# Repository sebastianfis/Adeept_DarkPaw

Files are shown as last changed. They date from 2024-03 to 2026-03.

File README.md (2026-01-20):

# DarkPaw

My personal take on improving the Adeept Dark Paw robot. Specific features I aim to tackle:
* **Correct Kinematic model**
* **AI supported object recognition/tracking**
* **Create an autonomous mode with dedicated behaviour**
* **Update the robot control interface**
* ~~**Voice recognition**~~ -> abandoned for now
* ~~**Sound generation**~~ -> abandoned for now

## UPDATE 2026-01-20:
As usual, it has been quite some time since I wrote the last update :sweat_smile: : 

### Hardware and hardware integration:
Long term testing showed, that the original 25 W power supply I intended to use, is too weak to run the Raspi5 with AI 
Hat and the ESP and the LEDs and all the servos. So I switched the power supply for something bigger and added a third 
18060 battery to power the whole thing for a decent amount of time (integration of the batteries pending). 

This led to a new issue: The ESP would not boot at the same time as the Raspi, which was never a problem before 
(Either its voltage ripple or some weird grounding issue of the power supply). I was able to solve this by starting 
up the ESP and using one of its outputs to switch on the RASPI via a MOSFET relays, so they now boot in sequence.

I also added a watchdog to the communication, so the ESP would detect a software crash on the Raspi side and stop 
instead of coniuting the last given command!

### Correct Kinematic model
I did some quite extensive testing on the C++ Implementation. The ESP32 works like a charm and is very reliable!

### AI supported object recognition/tracking
I added some code for object movement detection and in the process discovered, how unreliable the distance sensor 
readings are. Since on the Raspi 5 the Chip architecture is fairly different, hardware timed GPIO is not availlable.
Since regular GPIO timing in Python is not the most precise, I had to switch the distance sensor implementation to 
gpiod and add a bunch of stuff (floating average mean, rejection of false trigger events, sanity checks on timing and 
disatnce values). This is now as good, as it's going to get while running directly on a Pi. I also discovered that 
regular updates to the selected target data were missing, which is mandatory for the movement check.

### Robot control Interface website
Tested now and fully functional.

### What's next?
I am quite satisfied with the hardware as it is now (battery integration still pending). Also the C++ implentation is 
rather solid now and the Robt Control interface website (while it is not the most beautiful site) is very functional 
and highly responsive. From the original project goals, only **Create an autonomous mode with dedicated behaviour** is 
not complete yet, so that is where i can finally put my focus on.

## UPDATE 2025-04-26:
It has been quite some time since I wrote the last update and quite a few things have changed in the meantime :sweat_smile: : 

### Hardware and hardware integration: 
I designed some 3d printed parts to implement the changes I had to do in terms of hardware positioning. Check out the 
3d planning folder for the models, if you think you can use them.

### Correct Kinematic model
I did not have the time for a proper test of the C++ Implementation, yet. All I know right now is, that the serial 
communication works, so the C++ programm on the ESP is running fine, but I have not seen any actual movement from 
the robot yet. Have to do more tests on an isolated part of the setup to bugfix this.

### AI supported object recognition/tracking
Using the RASPI 5 and the AI HAT is very cool. I can now run the newest yolov11m model on the Hailo with ~18 fps 
framerate! 

### Robot control Interface website
While running the detection code locally gave me pretty good framerates, they plumeted to ~ 3 fps, when I was using 
the Webserver. Clearly streaming a MJPEG to a flask server is not the best choice for this task. In the end, I was 
forced to go a completely different route. There is a good reason, that both Hailo and Raspi Camera have a good load 
of GStreamer examples in ther repos. Gstreamer is probably one of the best choices, if you want to stream actual video 
(in contrast to an image sequence) over the web. But the python bindings for that are not well documented and the 
string based pipeline concept can be hard to grasp in the beginning. Since Hailo has a repo, where they only use 
gstreamer instead of Python for the whole chain of captureing an image, runing inference, annotation, and finally 
displaying/streaming, I gave that implementation a try. It turned out to be slower and not as pretty, as the 
implementation I had before using Raspicam2 and Supervision code, so I quickly gave up on that. So the new architecture 
is the following:

Raspicam2 -> inference & frame annoation as videosrc -> Gstreamer Pipeline -> WebRTC as videosink -> display on webpage

Took me a while to get this running, but it finally does! Bonus of this: Through WebRTC, asyncio and aiohttp I can also 
create a VERY responsive data channel for sending measurement data to the control interface and receive comands from 
it's elements.

## UPDATE 2024-12-08:
It has been quite some time since I wrote the last update and quite a few things have changed in the meantime :sweat_smile: : 

### Hardware
Time flies and when I started this project, the Google Coral Dev Board Mini or the Google Coral USB Accelerator were 
the only viable options for hardware accelerated AI applications on a size compatible with the Dark Paw robot frame. 
Well, there was the NVidia Jetson Nano, but I found that one too expensive and a bit too power hungry.

With the Raspberry Pi 5 and the Hailo AI HAT now on the market, there are is now actually a better option availlable 
considering the following criteria:
* Computing performance (in terms of TOPS)
* Model input tensor size (= image resolution) for yolo models
* Compatibility with peripheral equipment 
* Development comfort for video applications on a non-headless system
* Product support: There seems to have been no update to the Mendel Linux OS for the past 3 years...

Since I was never really quite satisfied with the object detection performance I was able to achieve with the Coral Dev Board Mini, I've chosen to switch the hardware for a Raspi 5 with an AI HAT. I felt the 13 TOPS variant would be suffcient and would safe some power vs. the 26 TOPS variant. This does not change anything on the planned "fore brain" / "hind brain" separation. I still think it is a good idea to do that separation!

I also added a HC-SR04 ultrasonic distance sensor. This will allow the robot to move in on an object down to a certain distance and even keep the distance for a moving object. And to make the robot a bit more expressive, I exchanged the blue LED of the front lens with a WS2812b multi-colour LED, that can be chained to the internal LEDs of the robot.

### Hardware Integration
Switching to the Raspi 5 / AI HAT Architecture has one downside though: It will be a lot bigger, than the Coral Dev Board Mini. So I had to do some re-arrangements of the robots insides: The LED-PCBs have to be moved further outside. The RASPI 5 and the AI HAT will be positionend on one side of the vertical electronics holder, while the ESP32 and the I2C PWM Servo Controller will be positioned on the other side. It's a close fit and I will probably curse a lot during cabling of this, but it should fit. I also won't ba able to fit the power supply inside the robot anymore, so I added an add-on part for the robot to carry a new DF-robot power supply PCB on its aft-side (this should come in handy in case of a robot spider uprising :joy:). Finally I added a holder to the HC-SR04 ultrasonic distance sensor to the upper front of the robot.

### Correct Kinematic model
I was able to port the python implementation to C++ and run it on an ESP32. It runs without crashing, and first tests on the calculated values are very promising. However, it is still lacking a real life test with the servos connected.

For communcation I will try using the good old serial connection first. This will run with minimal overhead both on the Raspi and the ESP32.

### AI supported object recognition/tracking
I was never really quite satisfied with the performance of the object detection models of the Google Coral Model Zoo on the Google Coral Mini board. The models were either too slow for real time video detection or accuracy was not satisfactory. So I went looking for more cutting edge object detection models and stumbled upon the yolo model series and later also ssd_spaghettinet. However, with these newer models some internal architecture of the Edge TPU limits the input tensor size, with which the model will still compile to run entirely on the Edge TPU to rather low resolutions. This means that object detection performance was better than with the models from the Coral model zoo, but false detection rates were still higher than what I had hoped for. Also, the limited resolution would make the robot a bit "short-sighted". It did work with an acceptable frame rate and I even got a tracker akgorithm to work, whcih would allow for keeping IDs of objects across different frames.

In the meantime, HAILO released a dedicated AI HAT for the Raspberry Pi 5, which does not have this limitation on input tensor size for modern object detection architectures. It also exceeds the TPU computing power by a factor > 3 (13 TOPS on the HAILO-8L vs. 4 TOPS on the Google Coral Dev Board Mini). So I decided to switch hardware (see above) and go ahead with a Raspi 5 equipped with an AI HAT. Getting the models to run in the Raspi Eco system was rather straightforward based on the examples in the picamera2 Repo and the HAILO Raspi 5 examples. This inculdes a object tracking algorithm with really awesome performance. 

### Autonomous mode with dedicated behaviour
No update on this (yet), except that I included 
* A "patrol" mode: The robot will go back and forth, with some tolerance on the angles, so it won't always go back and forth on the same path
* A "dance" mode: LEDs will set a light show and the robot will assume different poses at a certain rythm. This one is actually already finished :joy:

### Robot control Interface website
Oh boy! I put that off for quite some time. Understanding how the code of the Adeept Dark Paw original interface works was almost impossible to me. At some point I understood, that it was built in some sort of .js environment (I think Vue.js), but that did not make it much easier for someone with 0 experience in frontend development. In the end I gave up on trying to understand what the original code was trying to do and decided to do my own thing. 

So I started with designing a html/css website with Grapes.js and wrote my own javascript middleware. Putting that in contact with a flask server and responsive video streaming was everything but easy. There are numerous examples for simple video streaming out there, but most will reload the entire webiste over and over again, making registration of input commands a gamble at best. I finally found a solution for that and wrote a class-wrapped webserver implementation with thread-save command and data passing.

## UPDATE 2024-02-11:
After abondening the project for quite some time I took it up again. Here are some thoughts I had in the meantime 
(some of those caused my abandoning the project originally :sweat_smile:): 
### Hardware
Its pretty clear that the original Raspi based hardware would not be able to sustain all the features I'd like 
the robot to have. Checking the capabilities of availlable hardware, I decided that I would go with a Google 
Coral Mini board instead as main computation device, due to its on-board TPU, making it a great choice for 
AI applications.

However, after playing around with the Google Coral board I realized, that even with the on-board TPU there
would be issues with realization of all the stuff I wanted to implement, mainly because it would not be able 
to run several pre-compiled models (object recognition/tracking + Voice recognition + Sound generation) in 
parallel, but also since even running object recognition/tracking alone is already rather slow on the board.

So I had to narrow the project down on the points that were most important to me: 
* **Correct Kinematic model**
* **AI supported object recognition/tracking**
* ~~**Voice recognition**~~ -> abandoned for now
* ~~**Sound generation**~~ -> abandoned for now
* **Create an autonomous mode with dedicated behaviour**

Also, python is not the ideal programming language for "number crunching" which is essential for a 
correct kinematic model. With the lags I had seen on the Coral board, I decided to give the robot a "hind brain". 
Think about it: When you want to lift your extended arm, you do not think: 
* check shoulder angle, 
* check elbow angle
* calculate angle difference shoulder
* calculate angle difference elbow
* execute necessary angle changes

All you think is: "Lift and extend arm". All the rest: the fine adjustments, the translations into explicit 
control signals to all the muscles involved, the correct timing of the movements, etc... that's all done by 
your hind brain, without you having to take care of it. Why not mimick that separation of tasks in the robot 
as well? 

So the plan is to share the load between two computing entities: The main behaviour algorithm and AI supported 
object recognition/tracking would run on the "fore brain", which is the Google Coral board. As "hind brain" I am 
thinking about using somthing like an ESP32 (tbc). Running the number crunching kinematics on the ESP in C++ 
makes it efficient and fast. From there, Servo control should be pretty straight froward through a I2C connected 
PWM controller.

Considering how the two "brain-parts" will communicate with each other, I thought about using a serial exchange. 
But maybe I'll use the ROS2 environment instead, since it already provides a framework for communication of 
different computing nodes.

### Correct Kinematic model
If you checked out the implementation size of the kinematic model, you might wonder why It is so huge. 

The answer is simple: The availlable robot control packages I found out there while researching (e.g. ROS2) are 
limited to linear kinematic models. This is well and good for most applications, but the Adeept Dark Paw robots 
construction relies heavily on four bar linkage mechanisms (check out [this page](https://www.geogebra.org/m/BueCG9ch)
for an interactive animation).

Such a mechanism can be extremely strong, but is **highly non-linear**, especially with several of these 
actuators linked together, as it is the case here. Also, there are limits to the acutators, where further 
increase of the actuated parameter (aka servo angle) would actually lead to a decrease of the desired effect 
(e.g. retraction of the foot, even though a linear model would predict further extension).

So that's why I had to write the code from scratch to get a truely correct kinematic model. 

The model was already working quite well in Python, when I stopped working on the project, but I 
decided to add some details to the test visualizations (e.g. making them full 3d and build up on one another).

The next step will be to re-implement the tested python code in C++. In principle easy, but I have not yet 
written code containing class definitions in C++. But I'm hoping ChatGPT will help me out there :grin:

### AI supported object recognition/tracking
I already played around a bit with the Google Coral board and think it should work. I just have to find out, 
how I want to do the integration with the overall behavior algorithms, but more on that later

### Autonomous mode with dedicated behaviour
I actually started working on that part by drawing out the logic in a block flow diagram, but it is far 
from being finished...

## UPDATE 2024-02-23:
### Correct Kinematic model
Ok, so Kinematics works like a charm and I managed to implement all possible poses. However, I noticed 
a few unexpecetd challanges:

* From the "standard" leg position, movement range in y is VERY limited. I don't think that there's 
much can be done about it. It's a result of the kinematics. The only workaround for that is to let it do smaller 
steps in faster succession in y direction (move left/right). This also means, that I will not be able to make 
the robot circle an external reference point (like an identified object, it finds interesting and wants to 
take a closer look).
* The COG of the robot seems to be badly balanced. The poses, where it lifts a single leg are very 
unstable (and this means it does wobble a lot when walking as well). I'll have to do some more tests, 
this is true for all legs and if it can be counterbalanced. Another explanation might be the inertia of 
setting a pose too quickly. This can be easily changed, as the implementation allows for intermediate 
samples.

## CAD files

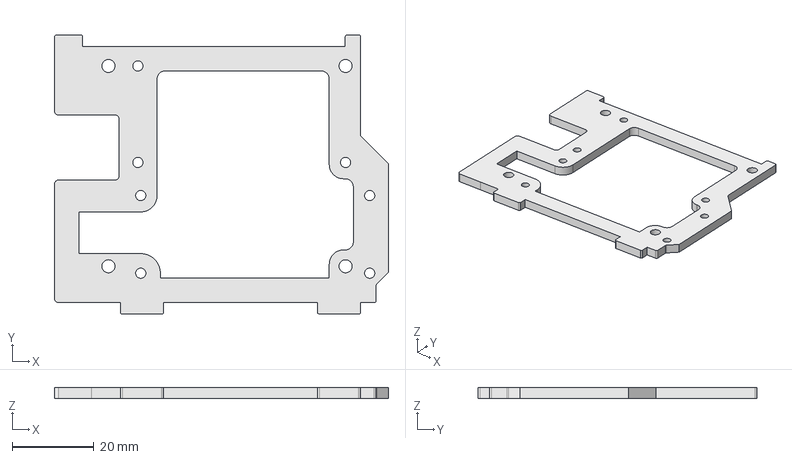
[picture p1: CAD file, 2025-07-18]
3d_planning/electronics_holder_new.FCStd
81.7 x 68.3 x 2.80 mm

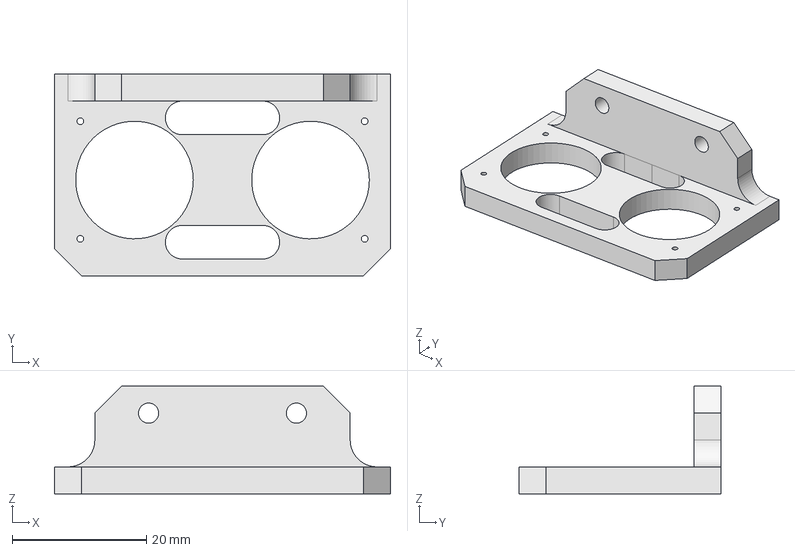
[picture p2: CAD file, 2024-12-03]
3d_planning/Ultrasonics_holder2.FCStd
50.0 x 30.0 x 16.0 mm

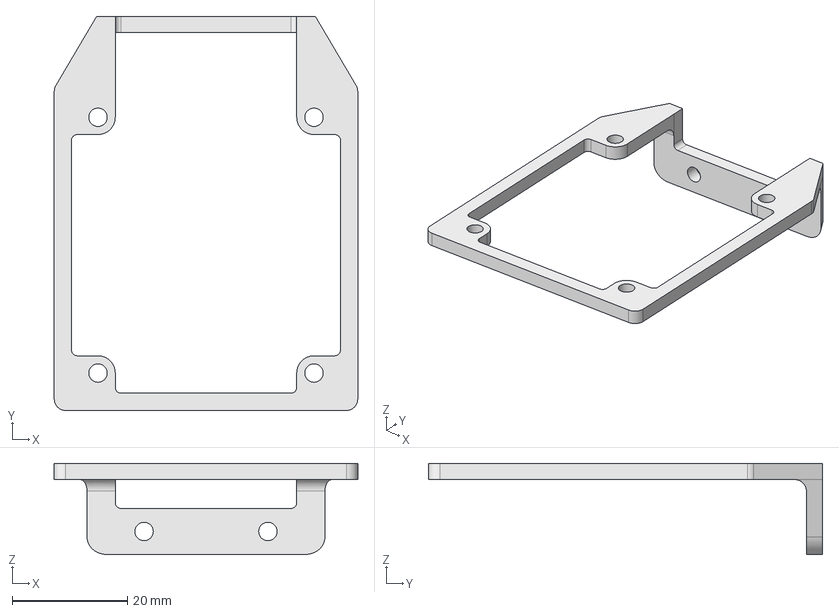
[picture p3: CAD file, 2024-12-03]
3d_planning/Powermodule_holder.FCStd
52.7 x 68.4 x 15.8 mm

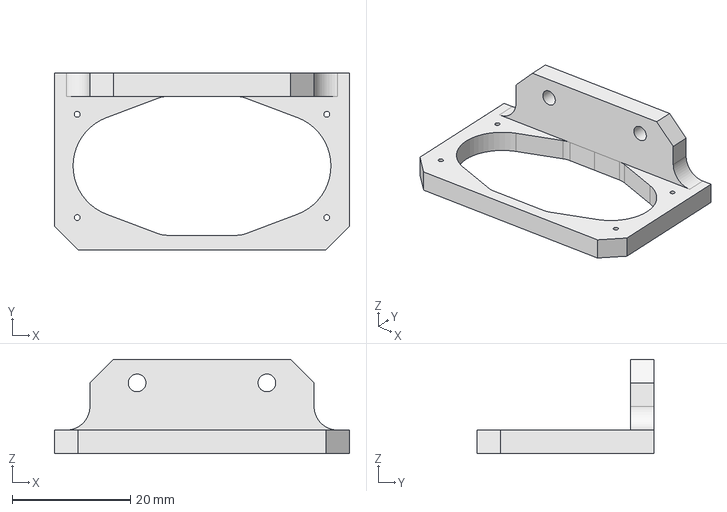
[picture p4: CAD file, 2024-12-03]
3d_planning/Ultrasonics_holder.FCStd
50.0 x 30.0 x 16.0 mm

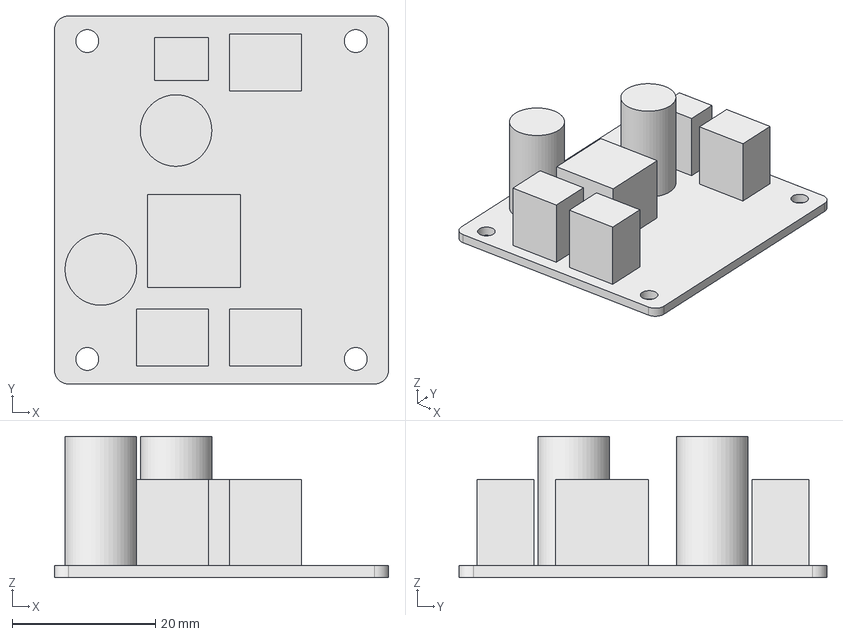
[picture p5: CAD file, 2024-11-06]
3d_planning/DF_robot_Powermodule.FCStd
46.7 x 51.4 x 19.7 mm

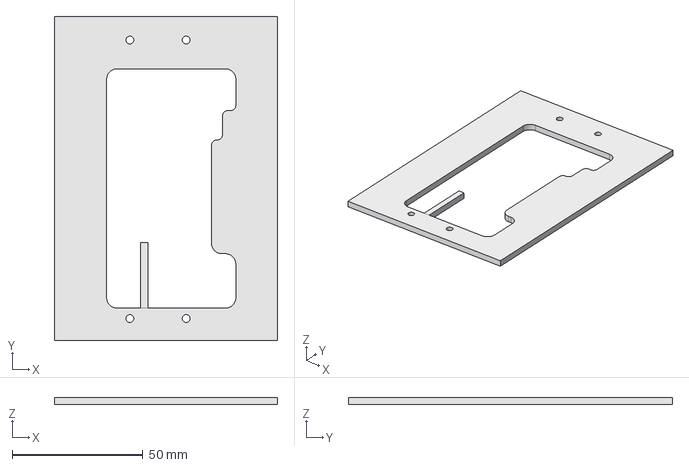
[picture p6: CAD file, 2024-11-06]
3d_planning/intermediate_boundary.FCStd
85.4 x 123.9 x 2.80 mm

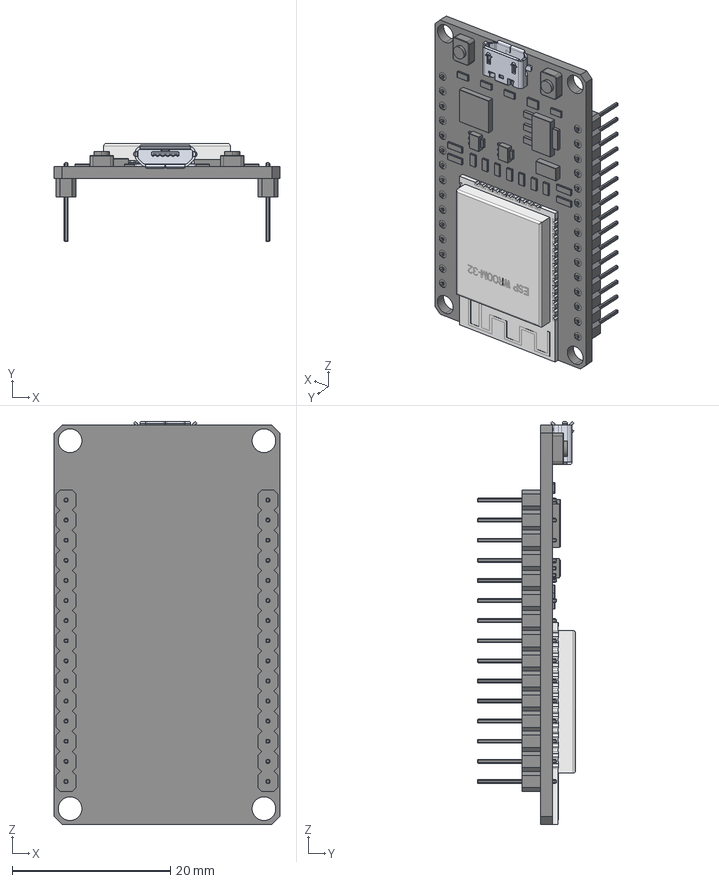
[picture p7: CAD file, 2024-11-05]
3d_planning/ESP32_Microcontrollerboard.FCStd
28.5 x 12.4 x 50.9 mm
micro_usb_47346-0001
ESP-WROOM-32
6.ESP-32_Predeterminado
6.ESP-32_Predeterminado001
6.ESP-32_Predeterminado002
6.ESP-32_Predeterminado003
6.ESP-32_Predeterminado004
6.ESP-32_Predeterminado005
6.ESP-32_Predeterminado006
6.ESP-32_Predeterminado007
6.ESP-32_Predeterminado008
6.ESP-32_Predeterminado009
6.ESP-32_Predeterminado010
6.ESP-32_Predeterminado011
6.ESP-32_Predeterminado012
6.ESP-32_Predeterminado013
6.ESP-32_Predeterminado014
6.ESP-32_Predeterminado015
6.ESP-32_Predeterminado016
6.ESP-32_Predeterminado017
6.ESP-32_Predeterminado018
6.ESP-32_Predeterminado019
6.ESP-32_Predeterminado020
6.ESP-32_Predeterminado021
6.ESP-32_Predeterminado022
6.ESP-32_Predeterminado023
6.ESP-32_Predeterminado024
6.ESP-32_Predeterminado025
6.ESP-32_Predeterminado026
6.ESP-32_Predeterminado027
6.ESP-32_Predeterminado028
6.ESP-32_Predeterminado029
6.ESP-32_Predeterminado030

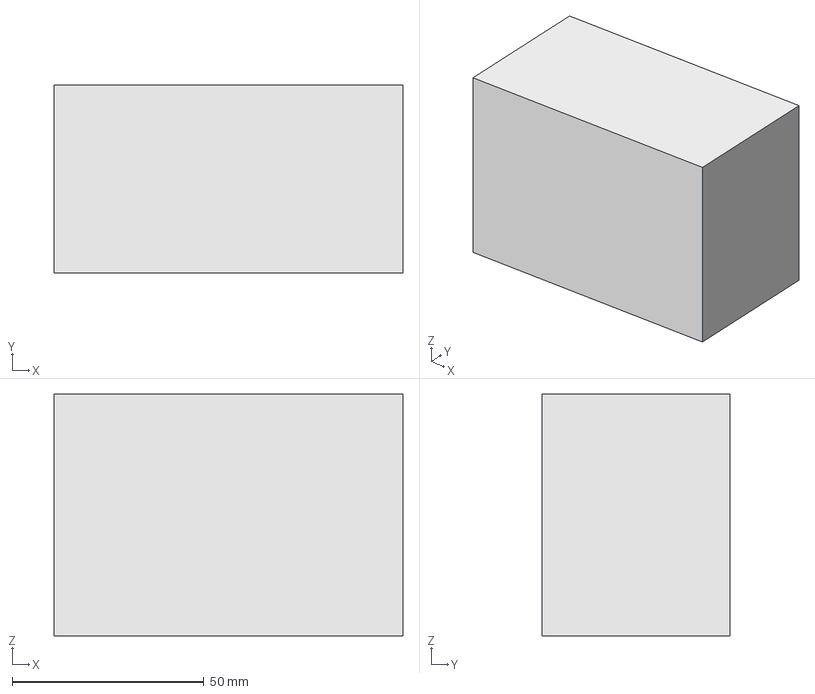
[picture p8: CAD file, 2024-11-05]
3d_planning/free_electronics_volume.FCStd
91.0 x 49.0 x 63.0 mm

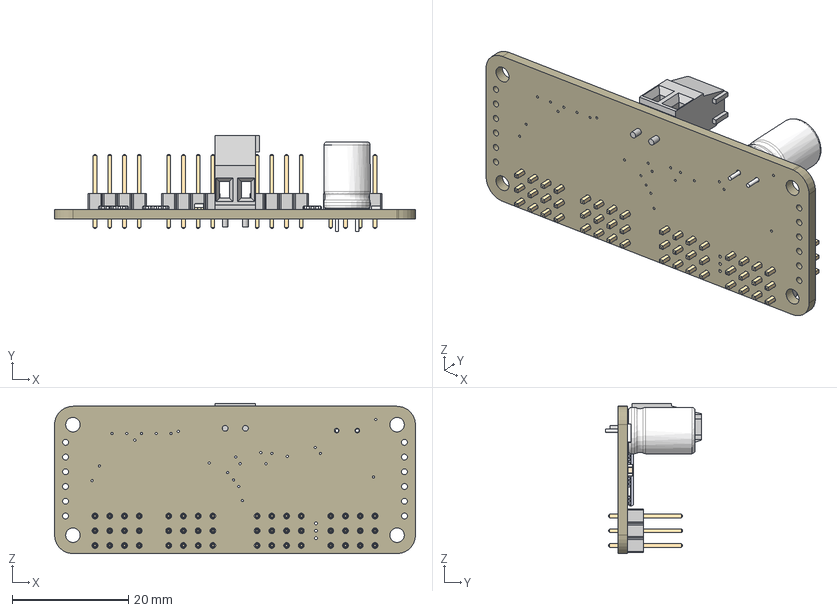
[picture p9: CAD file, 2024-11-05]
3d_planning/PCA9685_Servo_controller.FCStd
62.2 x 16.6 x 25.9 mm
Board
Pins
Pins001
Pins002
Pins003
Case
Pins005
Pins006
Pins007
Pins008
Case001
Pins010
Pins011
Pins012
Pins013
Case002
Pins015
Pins016
Pins017
Pins018
Case003
Pins020
Pins021
Pins022
Pins023
Case004
Pins025
Pins026
Pins027
Pins028
Case005
Pins030
Pins031
Pins032
Pins033
Case006
Pins035
Pins036
Pins037
Pins038
Case007
Pins040
Pins041
Pins042
Pins043
Case008
Pins045
Pins046
Pins047
Pins048
Case009
Pins050
Pins051
Pins052
Pins053
Case010
Pins055
Pins056
Pins057
Pins058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

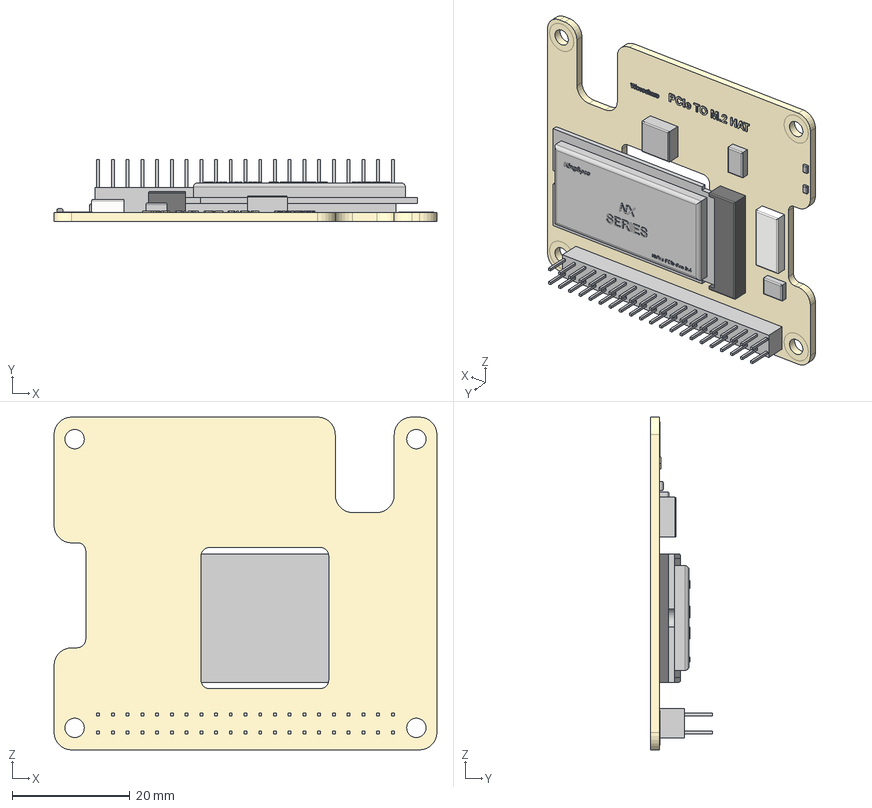
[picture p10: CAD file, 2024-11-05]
3d_planning/Raspi5_HAT.FCStd
65.0 x 10.6 x 56.5 mm
PCIe M.2 HAT Model
M.2 Connector
PCIe connector
Misc IC's
Misc IC's001
Misc IC's002
Misc IC's003
Misc IC's004
Misc IC's005
2242 NVMe

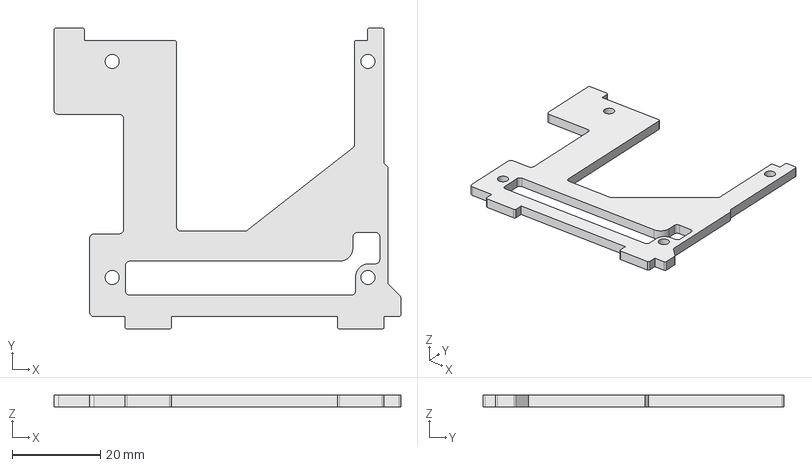
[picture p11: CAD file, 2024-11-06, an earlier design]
3d_planning/electronics_holder_old.FCStd
78.7 x 68.3 x 2.80 mm

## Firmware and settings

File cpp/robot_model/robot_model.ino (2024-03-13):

// #include "FourBarLinkage.h"
#include "math.h"
#include "SpiderLeg.h"
#include "Gait.h"
#include "Pose.h"

// FourBarLinkage linkage(42.5, 14.5, 38, 27.8, 90);
SpiderLeg RF(1, 1, "RF");
SpiderLeg LF(1, -1, "LF");
SpiderLeg RB(-1, 1, "RB");
SpiderLeg LB(-1, -1, "LB");

SpiderLeg *leg_list[] = {&RF, &LF, &RB, &LB};

// pose_n must be between 2 and 6!
short pose_n = 3;
float pose_goal[4][3];
Pose lift_LFL(leg_list, pose_goal, "LFL");

float update_freq = 50;
float step_height = 14;
bool inverted = false;

char direction = 'x';
float step_length = 80;
float velocity = 125;

// char direction = 'y';
// float step_length = 20;
// float velocity = 62.5;

// char direction = 't';
// float step_length = 70;
// float velocity = 109;

Gait move_forward(leg_list, update_freq, inverted, direction);

// void test_linkage() {
//   Serial.println(String("FourBarLinkage successfully initiated"));
//   Serial.println(String("phi_0 is: ")+ linkage.get_phi_0()/ M_PI * 180);
//   linkage.set_pwm_init(300, 1);
//   float phi_value = 92;  // Set your desired phi value
//   short pwm_result = linkage.calc_PWM(phi_value*M_PI/180);
//   Serial.println(String("PWM calculated. Phi actuator angle of ") + phi_value + " deg equals a PWM value of " + pwm_result);
//   float theta = linkage.calc_theta(phi_value*M_PI/180);
//   float phi_r = linkage.calc_phi(theta);
//   Serial.println(String("PWM value ") + pwm_result + " will result in  " + theta / M_PI * 180 + " deg actuator theta angle. Backward transform gives phi = " + phi_r/ M_PI * 180 + " deg.");
// }

// void test_legs() {
//   float phi[3];
//   float pos[3];
//   float phi_ret[3];
//   float result[3];
  
//   for (int leg = 0 ; leg < 4 ; leg++) {
//     String leg_name = leg_list[leg]->get_name();
//     leg_list[leg]->get_init_pos(result);
//     Serial.println(String("Initial foot position of ") + leg_name + ": x_f = " + result[0] + ", y_f = " + result[1] + ", z_f = " + result[2]);
//     Serial.println(String("SpiderLeg ") + leg_name + " successfully initiated");
//     leg_list[leg]->get_actuator_angles(phi);
//     Serial.println(String("Actuator angles succesfully read"));
//     leg_list[leg]->forward_transform(phi[0], phi[1], phi[2], &pos[0], &pos[1], &pos[2]);
//     Serial.println(String("Forward transform succesful!"));
//     Serial.println(String("actuator angles for ") + leg_name + ": " + phi[0] / M_PI * 180.0 + ", " + phi[1]  / M_PI * 180.0 + ", " + phi[2]  / M_PI * 180.0 + " will result in x_f = " + pos[0] + ", y_f = " + pos[1] + ", z_f = " + pos[2] + " foot position.");
//     leg_list[leg]->backward_transform(pos[0], pos[1], pos[2], &phi_ret[0], &phi_ret[1], &phi_ret[2]);
//     Serial.println(String("Backward transform succesful!"));
//     Serial.println(String("foot position of ") + leg_name + ": x_f = " + pos[0] + ", y_f = " + pos[1] + ", z_f = " + pos[2] + " correspont to actuator angles of "+ phi_ret[0] / M_PI * 180.0 + ", " + phi_ret[1]  / M_PI * 180.0 + ", " + phi_ret[2]  / M_PI * 180.0);
//   }
// }

// void test_pose() {
//   pose_n = 8;
//   for (short leg = 0; leg < 4; ++leg) {
//     float coords[3];
//     leg_list[leg]->get_cur_pos(coords);
//     Serial.println(String("foot position of ") + leg_list[leg]->get_name() + ": (" + coords[0] + ", " + coords[1] + ", " + coords[2] + ")");
//     for (short ii = 0; ii < 3; ++ii) {
//       pose_goal[leg][ii] = coords[ii];
//     }
//   }
//   pose_goal[1][2] -= 12;
  
//   lift_LFL.set_movement_goal(pose_goal);
//   Serial.println(String("movement goal successfully updated"));
//   float target[4][3];
//   lift_LFL.get_movement_goal(target);
//   for (short leg = 0; leg < 4; ++leg){
//     Serial.println(String("movement goal for ") + leg_list[leg]->get_name() + ": (" + target[leg][0] + ", " + target[leg][1]  + ", " + target[leg][2]  + ")");
//     Serial.flush();
//     }

//   lift_LFL.calc_pose_lists(6);
//   // lift_LFL.calc_pose_lists(3);
//   Serial.println(String(F("pose calculated successfully!")));
//   for (short leg = 0; leg < 4; ++leg){
//     for (short sample = 0; sample < pose_n; ++sample) {
//       Serial.println(String("coordinate sample of ") + leg_list[leg]->get_name() + ": (" + lift_LFL.get_coordinate_from_list(sample, leg, 0) + ", " + lift_LFL.get_coordinate_from_list(sample, leg, 1) + 
//                                                                                        ", " + lift_LFL.get_coordinate_from_list(sample, leg, 2) + ")");
//       Serial.flush();
//     }
//     for (short sample = 0; sample < pose_n; ++sample) {
//       Serial.println(String("PWM sample of ") + leg_list[leg]->get_name() + ": (" + lift_LFL.get_pwm_from_list(sample, leg, 0) + ", " + lift_LFL.get_pwm_from_list(sample, leg, 1) + 
//                                                                                 ", " + lift_LFL.get_pwm_from_list(sample, leg, 2) + ")");
//       Serial.flush();
//     }
//   }
// }

void test_gait() { 
  for (short init_step=0; init_step < 3; init_step++) {
    Serial.println(String("init step no ") + init_step + ":");
    for (short leg = 0; leg < 4; ++leg){
      for (short sample = 0; sample < move_forward.get_sample_no(); ++sample) {
        Serial.println(String("coordinate sample of ") + leg_list[leg]->get_name() + ": (" + move_forward.get_coordinate_from_list(init_step, sample, leg, 0, true) + ", " +
                                                                                          move_forward.get_coordinate_from_list(init_step, sample, leg, 1, true) + ", " +
                                                                                          move_forward.get_coordinate_from_list(init_step, sample, leg, 2, true) + ")");
        Serial.flush();
      }
      for (short sample = 0; sample < move_forward.get_sample_no(); ++sample) {
        Serial.println(String("PWM sample of ") + leg_list[leg]->get_name() + ": (" + move_forward.get_pwm_from_list(init_step, sample, leg, 0, true) + ", " +
                                                                                          move_forward.get_pwm_from_list(init_step, sample, leg, 1, true) + ", " +
                                                                                          move_forward.get_pwm_from_list(init_step, sample, leg, 2, true) + ")");
        Serial.flush();
      }
    }
  }
  for (short step=0; step < 4; step++) {
    Serial.println(String("step no ") + step + ":");
    for (short leg = 0; leg < 4; ++leg){
      for (short sample = 0; sample < move_forward.get_sample_no(); ++sample) {
        Serial.println(String("coordinate sample of ") + leg_list[leg]->get_name() + ": (" + move_forward.get_coordinate_from_list(step, sample, leg, 0, false) + ", " +
                                                                                          move_forward.get_coordinate_from_list(step, sample, leg, 1, false) + ", " +
                                                                                          move_forward.get_coordinate_from_list(step, sample, leg, 2, false) + ")");
        Serial.flush();
      }
      for (short sample = 0; sample < move_forward.get_sample_no(); ++sample) {
        Serial.println(String("PWM sample of ") + leg_list[leg]->get_name() + ": (" + move_forward.get_pwm_from_list(step, sample, leg, 0, false) + ", " +
                                                                                          move_forward.get_pwm_from_list(step, sample, leg, 1, false) + ", " +
                                                                                          move_forward.get_pwm_from_list(step, sample, leg, 2, false) + ")");
        Serial.flush();
      }
    }
  }

}

int main() {

 // test_linkage();
 // test_legs();
 // test_pose();
  test_gait();
  delay(5000);
}


void setup() {
  Serial.begin(115200);
  delay(1000);
  Serial.println("\n Starting...\n");
  Serial.flush();
  Serial.println(String("Gait succesfully created"));
  move_forward.init(step_length, step_height, velocity);
  Serial.println(String("Gait succesfully initialized"));

  // put your setup code here, to run once:
}

void loop() {
  main();  // put your main code here, to run repeatedly:
}

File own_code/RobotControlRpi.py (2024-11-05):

from threading import Thread, Event, Timer
from queue import Queue
import time
import numpy as np
import matplotlib.pyplot as plt
from SpiderKinematics import RobotModel

run_on_Raspi = True

if run_on_Raspi:
    import Adafruit_PCA9685
    from AdditionalEquipment import AccSensor, LED
    import RPi.GPIO as GPIO
    GPIO.setmode(GPIO.BCM)
    pwm = Adafruit_PCA9685.PCA9685()
    pwm.set_pwm_freq(50)
    led = LED()
    mpu6050 = AccSensor()
else:
    pwm = None
    led = None
    mpu6050 = None


translation_table = {'w': 'move_forward',
                     'x': 'move_backward',
                     'a': 'move_left',
                     'd': 'move_right',
                     'q': 'turn_left',
                     'e': 'turn_right'}

debug = False

# Create port dictionary:
ports = {'LF1_port': 0, 
         'LF2_port': 1, 
         'LF3_port': 2,
         'LB1_port': 3,
         'LB2_port': 4,
         'LB3_port': 5,
         'RF1_port': 6,
         'RF2_port': 7,
         'RF3_port': 8,
         'RB1_port': 9,
         'RB2_port': 10,
         'RB3_port': 11}

# Create init_pwm dictionary:
init_pwm = {'LF1_init_pwm': 305,
            'LF2_init_pwm': 325,
            'LF3_init_pwm': 330,
            'LB1_init_pwm': 295,
            'LB2_init_pwm': 300,
            'LB3_init_pwm': 285,
            'RF1_init_pwm': 295,
            'RF2_init_pwm': 285,
            'RF3_init_pwm': 290,
            'RB1_init_pwm': 365,
            'RB2_init_pwm': 340,
            'RB3_init_pwm': 345}


robot_model = RobotModel(init_pwm)
q = Queue()
rng = np.random.default_rng()


def set_pwm_values(step_dict: dict, jj, robot_mdl: RobotModel, pwm_driver):
    """
    function to immediatly set the PWM values of the robot actuators to values passed by a SpiderKinematic Gait class
    object gait list item. index jj denotes the point in the list of tuples, where to take the values from.
    After setting the PWM values, the current position tracking of the SpiderLeg class is updated for each robot leg.
    """
    if pwm_driver is not None:
        for x in ['F', 'B']:
            for y in ['L', 'R']:
                for ii in [0, 1, 2]:
                    pwm_driver.set_pwm(ports[y + x + str(ii+1) + '_port'], 0, step_dict[y + x + 'L_PWM'][jj][ii])
    robot_mdl.left_forward_leg.update_cur_phi(*step_dict['LFL'][jj])
    robot_mdl.left_backward_leg.update_cur_phi(*step_dict['LBL'][jj])
    robot_mdl.right_forward_leg.update_cur_phi(*step_dict['RFL'][jj])
    robot_mdl.right_backward_leg.update_cur_phi(*step_dict['RBL'][jj])


# class SequentialControl:
#     """
#     Note: This sequential implementation is intended to be the base for a later C++ imlementation
#     """
#     def __init__(self, robot_mdl: RobotModel, pwm_driver, gait_name='move_forward'):  # Adafruit_PCA9685.PCA9685):
#         self.run_time = 7
#         self.robot_model = robot_mdl
#         self.current_gait_no = 0
#         for gait in robot_mdl.gaits:
#             if gait.name == gait_name:
#                 self.current_gait_name = gait_name
#                 break
#             else:
#                 self.current_gait_name = None
#                 self.current_gait_no += 1
#         assert self.current_gait_name is not None, "given gait_name not implemented! Allowed gait_names are: " \
#                                                    "'move_forward', 'move_backward', 'move_right', 'move left', " \
#                                                    "'turn_right', 'turn_left'"
#         self.pwm_driver = pwm_driver
#         # self.pwm_driver.set_pwm(LF1_port, 0, LF1_init_pwm)
#         # self.pwm_driver.set_pwm(LF2_port, 0, LF2_init_pwm)
#         # self.pwm_driver.set_pwm(LF3_port, 0, LF3_init_pwm)
#         # self.pwm_driver.set_pwm(LB1_port, 0, LB1_init_pwm)
#         # self.pwm_driver.set_pwm(LB2_port, 0, LB2_init_pwm)
#         # self.pwm_driver.set_pwm(LB3_port, 0, LB3_init_pwm)
#         # self.pwm_driver.set_pwm(RF1_port, 0, RF1_init_pwm)
#         # self.pwm_driver.set_pwm(RF2_port, 0, RF2_init_pwm)
#         # self.pwm_driver.set_pwm(RF3_port, 0, RF3_init_pwm)
#         # self.pwm_driver.set_pwm(RB1_port, 0, RB1_init_pwm)
#         # self.pwm_driver.set_pwm(RB2_port, 0, RB2_init_pwm)
#         # self.pwm_driver.set_pwm(RB3_port, 0, RB3_init_pwm)
#         self.run_flag = True
#         self.init_gait = True
#         self.return_flag = False
#         self.reset_n = 12
#
#     def run(self):
#         start_time = time.perf_counter_ns()
#         last_exec_time = start_time
#         exec_freq = []
#         ii = 0
#         jj = 0
#         while self.run_flag:
#             now_time = time.perf_counter_ns()
#             if (now_time - last_exec_time) >= 1e9 / self.robot_model.update_freq:
#                 exec_freq.append(1e9 / (now_time - last_exec_time))
#                 if self.init_gait:
#                     step = self.robot_model.gaits[self.current_gait_no].init_gait_list[ii]
#                     set_pwm_values(step, jj, self.robot_model, self.pwm_driver)
#                     print('executing init step sequence [' + str(ii) + '][' + str(jj) + ']')
#                     jj += 1
#                     if jj == len(step['LFL_PWM']):
#                         jj = 0
#                         ii += 1
#                     if ii == len(self.robot_model.gaits[self.current_gait_no].init_gait_list):
#                         ii = 0
#                         self.init_gait = False
#                 else:
#                     step = self.robot_model.gaits[self.current_gait_no].gait_list[ii]
#                     set_pwm_values(step, jj, self.robot_model, self.pwm_driver)
#                     print('executing step sequence [' + str(ii) + '][' + str(jj) + ']')
#                     jj += 1
#                     if jj == len(step['LFL_PWM']):
#                         jj = 0
#                         ii += 1
#                     if ii == len(self.robot_model.gaits[self.current_gait_no].gait_list):
#                         ii = 0
#
#                 # print('ran for {} seconds'.format((now_time - start_time) / 1e9))
#
#                 last_exec_time = now_time
#             if now_time - start_time >= 1e9 * self.run_time:
#                 print('movement timeout! Executing return step sequence')
#                 last_exec_time = now_time
#                 ii = 0
#                 jj = 0
#                 self.run_flag = False
#
#         print('Movement stopped!')
#         reset_gait = self.robot_model.calc_reset_move()
#         print('Movement terminated after {} seconds. Executing reset step sequence.'.format(self.run_time))
#         self.return_flag = True
#         ii = 0
#         jj = 0
#         while self.return_flag:
#             now_time = time.perf_counter_ns()
#             if (now_time - last_exec_time) > 1e9 / self.robot_model.update_freq:
#                 timestamp = (now_time - start_time) / 1e9
#                 exec_freq.append(1e9 / (now_time - last_exec_time))
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

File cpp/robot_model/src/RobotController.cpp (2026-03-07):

#include "RobotController.h"
#include "Arduino.h"
#include "RobotModel.h"
#include <Adafruit_MPU6050.h>
#include <Adafruit_Sensor.h>
#include <Adafruit_PWMServoDriver.h>
#include <Preferences.h>
#include <sstream>

#define SERVOMIN   100   // 0 bis 4096 - try and error
#define SERVOMAX   560   // 0 bis 4096 - try and error
#define SERVO_FREQ 50    // Analog servos run at ~50 Hz updates
#define EMEA 0.1 // Measurement Uncertainty for Kalman Filter
#define EEST 0.01 // Estimation Uncertainty for Kalman Filter
#define PROCNOISE 0.03 // Process Noise for Kalman Filter
#define P 1 // proportional parameter for controller
#define I 0.00001 // integral parameter for controller
// #include "FunctionTests.h"
#define DEBUG 1 //debug mode


// --- Serial command buffer ---
const byte numChars = 10;  /**< Maximum length of incoming serial commands */
char receivedChars[numChars]; /**< Serial command buffer */

// --- Preferences storage for actuator parameters ---
Preferences preferences;

/**
 * @brief PWM pin mapping for each actuator on each leg
 * port_list[leg_no][actuator_no]
 */
const short port_list[4][3] = {{9, 8, 7},    /**< Leg 0 (RF) */
                               {15, 14, 13}, /**< Leg 1 (LF) */
                               {6, 5, 4},    /**< Leg 2 (RB) */
                               {12, 11, 10}};/**< Leg 3 (LB) */


/**
 * @brief Initial PWM values for each actuator
 */
const short init_pwm[4][3] = {{290, 280, 295},
                              {295, 290, 270},
                              {340, 315, 325},
                              {275, 305, 310}};

/**
 * @brief Actuator direction mapping (1 = normal, -1 = reversed)
 */
const short actuator_direction[4][3] = {{1, -1, 1},
                                        {-1, 1, -1},
                                        {1, 1, -1},
                                        {-1, -1, 1}};

/**
 * @brief Constructor for RobotController
 * @param leg_list Array of 4 SpiderLeg pointers
 * @param serial Pointer to HardwareSerial object for communication
 * @param pwm Pointer to Adafruit_PWMServoDriver for servos
 * @param mpu Pointer to Adafruit_MPU6050 sensor
 *
 * Initializes controller variables and hardware references.
 */
RobotController::RobotController(SpiderLeg *leg_list[4],
                                 HardwareSerial* serial,
                                 Adafruit_PWMServoDriver* pwm,
                                 Adafruit_MPU6050* mpu):
robot_model(leg_list) {
    // Save hardware references
    this->stream = serial;
    this->leg_list[0] = leg_list[0];
    this->leg_list[1] = leg_list[1];
    this->leg_list[2] = leg_list[2];
    this->leg_list[3] = leg_list[3];
    // Initialize control state variables
    this->current_gait_no = -1;       /**< No gait active initially */
    this->current_pose_no = -1;       /**< No pose active initially */
    this->cur_sample = 0;             /**< Current sample index in step */
    this->cur_step = 0;               /**< Current step index in gait/reset */
    this->bpm_setting = 80;           /**< Default dance BPM */
    this->velocity_setting = 100;     /**< Default gait speed percentage */
    this->change_v_flag = false;      /**< Flag to update velocity */
    this->init_flag = false;          /**< Flag for init gait */
    this->reset_flag = false;         /**< Flag for reset step execution */
    this->pose_reached_flag = false;  /**< Flag indicating pose reached */
    this->dance_flag = false;         /**< Flag indicating dance mode active */
    this->balance_flag = false;       /**< Flag indicating balance mode active */
    this->last_command_ms = 0;        /**< Initialize timekeeping since last command */
    this->COMMAND_TIMEOUT_MS = 1000;  /**< Timeout for communication failure detection */
    this->comms_lost = false;         /**< Flag indicating communication failure */
    this->controller_armed = false;   /**< Flag indicating armed state of the ESP for movement */
    this->last_controller_armed = false; /**< Previous controller armed state */
    this->last_balance_flag = false;    /**< Previous balanace flag state */
    this->last_dance_flag = false;      /**< Previous dance flag state */
    this->last_gait_no = -2;            /**< Previous gait no */
    this->last_pose_no = -2;            /**< Previous pose no */

    // Save hardware interfaces
    this->pwm = pwm;
    this->mpu = mpu;
}

/**
 * @brief Initialize robot controller, PWM driver, MPU sensor, and leg actuators
 *
 * Sets up serial communication, PWM frequency, actuator PWM values,
 * initializes MPU6050 and calculates initial pose of robot.
 */
void RobotController::init(){
    // Begin serial communication
    this->stream->begin(115200);
    // Calculate PWM update period in microseconds
    this->pwm_update_period = round(1e6/SERVO_FREQ);
    // Reset timers and control variables
    this->time_now = 0;
    this->sensor_timer = 0;
    this->last_theta_x = 0;
    this->last_theta_y = 0;
    this->integral_x = 0;
    this->integral_y = 0;
    // Initialize PWM driver
    this->pwm->begin();
    this->pwm->setOscillatorFrequency(24700000);
    this->pwm->setPWMFreq(SERVO_FREQ);
    if (DEBUG) {
        this->stream->println(String("PWM driver successfully initialized!"));
    }

    // Begin non-volatile storage for actuator settings
    preferences.begin("act_data", false);

    // Store default actuator PWM and direction values if not already stored
    for (short leg_no = 0; leg_no < 4; ++leg_no){
        for (short act_no = 0; act_no <3; ++act_no) {
            if (!preferences.isKey((String("init_pwm_") + leg_no + "" + act_no).c_str())) {
                preferences.putShort((String("init_pwm_") + leg_no + "" + act_no).c_str(), init_pwm[leg_no][act_no]);
            }
            if (!preferences.isKey((String("act_dir_") + leg_no + "" + act_no).c_str())) {
                preferences.putShort((String("act_dir_") + leg_no + "" + act_no).c_str(), actuator_direction[leg_no][act_no]);
            }
        }
    }

    // Set initial PWM for all actuators
    this->set_init_pwm();

    delay(100); // wait for hardware to stabilize
    // Initialize MPU6050 sensor
    this->mpu->begin();
    this->mpu->setGyroRange(MPU6050_RANGE_250_DEG);
    this->mpu->setFilterBandwidth(MPU6050_BAND_21_HZ);
    this->evaluate_mpu_errors(); // compute initial sensor bias
    if (DEBUG) {
         this->stream->println(String("MPU6050 sensor successfully initialized!"));
    }
}
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

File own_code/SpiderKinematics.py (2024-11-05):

# This code is lagacy only. All implementaions herein have been ported to C++ to run directly on the ESP

import numpy as np
import matplotlib.pyplot as plt


class FourBarLinkage:
    """
    Class to implement a four bar linkage of such a type:

                  l_ab
             A __________ B
             /            \
     l_sa   /              \ l_gb
           /  phi     theta \
         S ----------------- G
                l_sg
    S denotes the servo axis position. G the position of the joint axis. The angles phi and theta are defined positive
    from the connecting line between servo axis S and joint axis G.
    """

    def __init__(self, l_sg, l_sa, l_ab, l_gb, phi_0: float = 90):
        self.l_sg = l_sg
        self.l_sa = l_sa
        self.l_ab = l_ab
        self.l_gb = l_gb
        self.phi_max = np.pi
        self.phi_min = -np.pi
        self.theta_max = np.pi
        self.theta_min = -np.pi
        self.cur_phi = np.deg2rad(phi_0)
        self.calc_limits(self.cur_phi)
        self.cur_theta = self.calc_theta(self.cur_phi)
        self.phi_0 = self.cur_phi
        self.pwm_0 = 330
        self.actuator_direction = 1

    def set_pwm_init(self, pwm_value, actuator_direction):
        """
        method to set the initial pwm value, at which the actuator angle is phi_0 and the correct direction!
        """
        assert actuator_direction == 1 or actuator_direction == -1, "actuator_direction must be 1 or -1!"
        self.pwm_0 = pwm_value
        self.actuator_direction = actuator_direction

    def calc_PWM(self, phi: float) -> int:
        """method to calculate pwm value from set phi value (in rad)"""
        pwm_value = self.pwm_0 + self.actuator_direction * (phi - self.phi_0) * 460 / np.pi
        if pwm_value < 100:
            pwm_value = 100
        elif pwm_value > 560:
            pwm_value = 560
        return int(pwm_value)

    def calc_theta(self, phi):
        """
        method to calculate theta (in rad) from phi (in rad)
        """
        l_ag = np.sqrt(self.l_sa ** 2 + self.l_sg ** 2 - 2 * self.l_sa * self.l_sg * np.cos(phi))
        assert self.phi_min <= phi <= self.phi_max, \
            'Movement not possible, because l_ag > l_ab + l_gb: {0} > {1} + {2}'.format(l_ag, self.l_ab, self.l_gb)
        # avoid errors due to rounding issues (e.g. arccos(1.00000000000000004) by clipping to -1, 1 range)
        theta_1 = np.arccos(np.clip((self.l_sg ** 2 + l_ag ** 2 - self.l_sa ** 2) / (2 * self.l_sg * l_ag), -1, 1))
        theta_2 = np.arccos(np.clip((self.l_gb ** 2 + l_ag ** 2 - self.l_ab ** 2) / (2 * self.l_gb * l_ag), -1, 1))
        theta = theta_1 + theta_2
        return theta

    def calc_phi(self, theta):
        """
        method to calculate phi (in rad) from theta (in rad)
        """
        l_bs = np.sqrt(self.l_gb ** 2 + self.l_sg ** 2 - 2 * self.l_gb * self.l_sg * np.cos(theta))
        assert self.theta_min <= theta <= self.theta_max, \
            'Movement not possible, because l_bs > l_ab + l_sa: {0} > {1} + {2}'.format(l_bs, self.l_ab, self.l_sa)
        # avoid errors due to rounding issues (e.g. arccos(1.00000000000000004) by clipping to -1, 1 range)
        phi_1 = np.arccos(np.clip((self.l_sg ** 2 + l_bs ** 2 - self.l_gb ** 2) / (2 * self.l_sg * l_bs), -1, 1))
        phi_2 = np.arccos(np.clip((self.l_sa ** 2 + l_bs ** 2 - self.l_ab ** 2) / (2 * self.l_sa * l_bs), -1, 1))
        phi = phi_1 + phi_2
        return phi


    def calc_limits(self, phi_0):
        """Sets the movement limits to meaningful values defined by a) boundaries of the actuator of +/- 90 deg from the
        initial position. b) by calculating the angle at which the connected bars are in a straight line. Further
        movement would then revert the direction of a change in the other angle!"""
        l_ag_max = self.l_ab + self.l_gb
        phi_max = np.arccos(np.clip((self.l_sa ** 2 + self.l_sg ** 2 - l_ag_max ** 2) / (2 * self.l_sa * self.l_sg),
                                    -1, 1))
        if phi_max > phi_0 + np.pi / 2:  # Correct value, if it is out of servo movement range!
            self.phi_max = phi_0 + np.pi / 2
        else:
            self.phi_max = phi_max

        self.theta_min = self.calc_theta(self.phi_max)

        l_bs_max = self.l_ab + self.l_sa
        theta_max = np.arccos(np.clip((self.l_gb ** 2 + self.l_sg ** 2 - l_bs_max ** 2) / (2 * self.l_gb * self.l_sg),
                                      -1, 1))
        # avoid errors due to rounding issues (e.g. arccos(1.00000000000000004)) by clipping to -1, 1 range)
        self.theta_max = theta_max
        phi_min = self.calc_phi(self.theta_max)
        if phi_min < phi_0 - np.pi / 2:
            self.phi_min = phi_0 - np.pi / 2
        else:
            self.phi_min = phi_min

    def plot_current_state(self, ax=None, linestyle='-', color='blue', cs_rot_angle: float = 30,
                           g_offset=None, inv_x=1, inv_y=1, inv_z=1, act1_theta=0):
        if g_offset is None:
            g_offset = [0, 0, 0]
        if ax is None:
            fig = plt.figure()
            ax = fig.add_subplot(111, projection='3d')
        r_list = np.array([0, -self.l_sg, -self.l_sg + self.l_sa * np.cos(self.cur_phi),
                           - self.l_gb * np.cos(self.cur_theta), 0])
        z_list = np.array([0, 0, self.l_sa * np.sin(self.cur_phi),
                           self.l_gb * np.sin(self.cur_theta), 0])
        rot = np.array([[np.cos(np.deg2rad(-cs_rot_angle)), -np.sin(np.deg2rad(-cs_rot_angle))],
                        [np.sin(np.deg2rad(-cs_rot_angle)), np.cos(np.deg2rad(-cs_rot_angle))]])
        [r_list, z_list] = np.dot(rot, [r_list, z_list])
        x_list = inv_x * r_list * np.cos(act1_theta) + g_offset[0]
        y_list = inv_y * r_list * np.sin(act1_theta) + g_offset[1]
        z_list = inv_z * z_list + g_offset[2]
        ax.plot(x_list, y_list, z_list, linestyle=linestyle, color=color)
        return ax
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

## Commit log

2022-03-08 initial commit of kinematic model
2024-02-11 changed to 3d and corrected visualization of single leg
    [Model_tests.py, SpiderKinematics.py]
2024-02-11 changed to 3d and corrected visualization of single_step
    [Model_tests.py, SpiderKinematics.py]
2024-02-11 - implemented update of current data functions for the SpiderLeg class - included leg display in gait_implementation_test visualization
2024-02-11 Corrected gait PWM lists to actually contain PWMs instead of phis!
    [Model_tests.py, SpiderKinematics.py]
2024-02-11 - changed the gaits in RobotModel class to be listed and have an identifiable name parameter (will make extension of possible gaits more easy in the future) - started preparing the external run contr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
2024-02-12 - unified robot leg designations everywhere to by refactoring the designations to left/right_forward/backward_leg - implemented PWM update logic both for sequential implementation and thread based im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
2024-02-13 - updated port numbers and servo calibration - corrected reset move calculation
    [SpiderKinematics.py, external_run_control_test.py]
2024-02-17 - found an ambiguity in the FourBarlinkage implementation (not corrected, yet!) - corrected Servo PWM scaling
    [Model_tests.py, SpiderKinematics.py]
2024-02-18 - No ambiguity in FourBarLinkage angle calculation... - corrected Servo Init PWM according to new Servo PWM scaling
    [Model_tests.py, SpiderKinematics.py, external_run_control_test.py]
2024-02-18 - Fixed reset move calculation (Added virtual position and angle updates in between updates steps)
    [Model_tests.py, SpiderKinematics.py, external_run_control_test.py]
2024-02-18 - Automated max. velocity calculation - Corrected step sample calculation from velocity
    [Model_tests.py, SpiderKinematics.py, external_run_control_test.py]
2024-02-19 - Added some tolerance to the FourBarLinkage angle min max check - Added rounding before arcos functions in the FourBarLinkage class to avoid errors from machine accuracy buildup
    [Model_tests.py, SpiderKinematics.py]
2024-02-20 - Removed tolerance to the FourBarLinkage angle min max check again, as it prooved to be way too unpredictable
    - Added some documentation to SpiderLeg and RobotModel methods
    - implemented methods to get and set robot body angles
    [Model_tests.py, SpiderKinematics.py, external_run_control_test.py]
2024-02-20 - Removed tolerance to the FourBarLinkage angle min max check again, as it prooved to be way too unpredictable - Added some documentation to SpiderLeg and RobotModel methods - implemented methods to 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
    [Model_tests.py, SpiderKinematics.py, external_run_control_test.py]
2024-02-20 - Corrected x and y positions in calc_leg_pos_from_body_angles method
    [SpiderKinematics.py]
2024-02-22 - Corrected y axis orientation in plot - Added method to calculate intermediate steps for setting a pose - Added pose with each leg lifted
    [Model_tests.py, SpiderKinematics.py, external_run_control_test.py]
2024-02-23 - Corrected some init values and tested poses
    [SpiderKinematics.py, external_run_control_test.py]
2024-02-23 - Corrected some init values and tested poses - doc update
    [Model_tests.py, SpiderKinematics.py, external_run_control_test.py]
2024-02-24 - Added init_pwm to end of gait reset - Added python file for servo calibration
    [calibrate_servos.py, external_run_control_test.py]
2024-02-24 - Corrected bug in gait reset move
    [SpiderKinematics.py]
2024-02-25 - Replaced rounding in all arcos functions with clipping the input to [-1, 1] range
    [SpiderKinematics.py]
2024-02-26 - Corrected missing string parts in port call and init_pwm
    [external_run_control_test.py]
2024-02-27 - Corrected errors in C++ implementations of SpiderLeg.cpp and FourBarLinkage.cpp
    [FourBarLinkage.cpp, SpiderLeg.cpp]
2024-02-27 - Removed struct definition (not needed) and added method to read out the actuator angles from without the SpiderLeg class
2024-02-27 - Added correct header definition to C++ classes - Corrected C++ FourBarLinkage implementation - SpiderLeg implementation not tested yet
    [FourBarLinkage.cpp, SpiderLeg.cpp, robot_model.ino]
2024-02-28 - Corrected and tested SpiderLeg C++ implementation - FourBarLinkage and SpiderLeg have now both been succesfully tested on an ESP32-WROOM-32 module
    [SpiderLeg.cpp, robot_model.ino]
2024-03-01 - Reduced variable storage space in CPP by changing some values from double to float and fixing some SpiderLeg parameters as const.
    [FourBarLinkage.cpp, SpiderLeg.cpp, robot_model.ino]
2024-03-13 - Implemented the gait generation. Note : Actual gait generation still crashes the program -> find out why
    [Gait.cpp, Pose.cpp, robot_model.ino]
2024-03-29 - Implemented Acceleration sensor and Distance sensor classes
2024-03-31 - Updated Distance sensor class, implemented LED class
2024-04-01 - Made cont. meaurement of Dist sensor thread safe. Introduced sample averaging for AccSensor
2024-04-01 - Adapted LED class, cleanedup and made thread safe
2024-04-02 - Included LED test in robot control
2024-04-03 - Adapted LED class
2024-04-03 - Removed lift leg from poses
2024-04-03 - Switched position of cpp code into sub-directories
2024-04-09 - Started implementing RobotModel class in C++ - Fixed bug in Gait class, that resulted in calculations of the samples in turn movements being wrong after velocity changes
    [Gait.cpp, Pose.cpp, RobotModel.cpp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]
2024-11-05 - Implemented methods for calibrating the servos (ESP Client) - Added 3D files for electronic layout planning - Old code for direct control transferred to "RobotControlRpi.py" (legacy) - Started work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
    [DF_robot_Powermodule.FCStd, ESP32_Microcontrollerboard.FCStd, PCA9685_Servo_controller.FCStd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]
2024-11-05 - Removed worker threads were not necessary anymore due to computation running on ESP. - Added code to read out and store distance measurements
2024-11-06 - Updated 3D planning
    [DF_robot_Powermodule.FCStd, electronics_holder_new.FCStd, electronics_holder_old.FCStd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]
2024-11-08 - optimzed Mass of new electronic holders - Added test for LED class
    [electronics_holder_new.FCStd]
2024-11-12 - started rework of Control interface
    [AdditionalEquipment.py, AppServer.py, RobotController.cpp]
2024-11-17 - Started woking on HAILO integration - First try to stream video via socketio
2024-11-18 - Switched from Flask Server to WebRTC based Architecture for enhanced video capabilities
2024-11-20 - Switched to flask with own streaming server port
2024-11-20 - Corrected paths for static serving
    [AppServer.py]
2024-11-21 - Corrected error in picamera2 call
    [AppServer.py]
2024-11-21 - Corrected error in index javascript
    [AppServer.py]
2024-11-22 - Tried exchanging mjpeg encoder with jpeg encoder for better framerate
2024-11-22 - Added functions to read temperature, CPU load and RAM usage, added test function for Distance sensor
2024-11-22 - Increased default timer vale of distance sensor to 300 ms
2024-11-22 - Reverted default timer vale of distance sensor to 100 ms
    [AdditionalEquipment.py]
2024-11-23 - Switched preprocessing, as simultaneous capturing does not work for not overlapping frame sizes!
    [detection_engine.py]
2024-11-23 - Corrected postprocessing code
    [detection_engine.py]
2024-11-24 - Added smaller models for better FPS - Corrected FPS display
    [detection_engine.py]
2024-11-24 - Corrected FPS display
    [detection_engine.py]
2024-11-24 - Switched implementation for argsort of confidence list
2024-11-24 - Reverted to yolov10b model
    [detection_engine.py]
2024-11-25 - Included frame rate limitation for test
2024-11-26 - Working state at ~ 30 fps with tracker and correct frame size passed to preview window
    [detection_engine.py]
2024-11-26 - Corrected color transfrom for detection to BGR
    [detection_engine.py]
2024-11-26 - Included Lock() and get_results method for thread safe access
2024-11-27 - wrote DefaultModeNetwork class (highest hierarchy) - integrated lights and distance sensor in dmn
2024-11-27 - Removed LED support for now.
2024-12-01 - Exchanged pi5neo library with rpi5_ws2812 due to timing problems
    [AdditionalEquipment.py]
2024-12-03 - started integration of velocity setting
2024-12-14 - corrected update_detection_counter implementation to also include initial detections completely - implemented method to center target in FOV
    [DMN.py]
2024-12-30 - corrected fps calculation dampening
    [detection_engine.py]
2025-01-12 - corrected read out of serial connection
    [MotionControl.py]
2025-04-17 - Switched detection engine implementation to instead work with gstreamer. Hopefully this will clear the issue with the low online video frame rate!
    [AppServer.py, DMN.py, detection_engine.py]
2025-04-18 - Switched detection engine implementation to instead work with gstreamer. Hopefully this will clear the issue with the low online video frame rate! - Added and modified webrtc_sendrecv.py from https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
    [AppServer.py, detection_engine.py]
2025-04-26 - Video is fixed and data channel is set up! Data display not working yet
    [AppServer.py]
2025-04-26 - Fixed data channel issue. Next: Fix data communication!
    [AppServer.py]
2025-04-26 - Data communication is fixed now!!!
    [AppServer.py, DMN.py, detection_engine.py]
2025-04-27 - Changed top class level from switched additional equipment from Thread to Process
2025-04-27 - Updated LED handling
2025-05-07 - Bugfixed servo code
    [DMN.py, FunctionTests.cpp, Gait.cpp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]
2025-05-10 - Bugfixed cpp code to working version. Only remaining issue is smoothness of balance feature
    [DMN.py, RobotController.cpp, RobotModel.cpp]
2025-05-12 - Improved smoothness of balance feature. Still open: Test of PI-control implementation, test of correct parsing of "cp" commands
    [RobotController.cpp, main.cpp]
2025-05-18 - Updated PWM start values
2025-05-18 - Started remaking detector to run in different process, not thread!
2025-05-19 - Tried code for adaptive detection frame adjustment
2025-05-19 - Reverted parts of the code to old version for better inference performance!
    [AppServer.py, DMN.py, detection_engine.py]
2025-07-18 - corrected Acutator numbers!
    [electronics_holder_new.FCStd]
2025-07-18 - corrected Actuator numbers! Corrected turn left/right direction!
    [MotionControl.py]
2025-07-20 - Corrected turn left/right direction in ESP Firmware, added possibility to start the Raspi from the ESP using a MOSFET Relay
    [MotionControl.py, RobotController.cpp, main.cpp]
2025-07-26 BIG REFACTOR: - Removed last traces of old code - changed directory layout - added python scripts for automatic system setup, create and remove autostart function
2026-01-06 -Moved Acceleration sensor python code to legacy folder (now handled by ESP32)
2026-01-09 -Tried reimplementation of distance sensor using pigpio
2026-01-09 -Tried reimplementation of distance sensor
2026-01-10 -Tried reimplementation of distance sensor without state machine
2026-01-11 -Distance Sensor: Replaced time.perf_counter() with event.timestamp for better accuracy
    [AdditionalEquipment.py, test_HC-SR04.py]
2026-01-11 Revert "-Tried reimplementation of distance sensor without state machine"
    This reverts commit ba57194eb8557a910d438e769a34eeae41e702b3.
    [AdditionalEquipment.py]
2026-01-11 Revert "Revert "-Tried reimplementation of distance sensor without state machine""
    This reverts commit 97928871c9fc9a45c3fc72f4dd32be6aa4966f71.
    [AdditionalEquipment.py]
2026-01-11 Revert "Revert "Revert "-Tried reimplementation of distance sensor without state machine"""
    This reverts commit 9fe80138c28f16dbd1c63b08ce20d932ed36adbd.
    [AdditionalEquipment.py]
2026-01-11 Revert "-Distance Sensor: Replaced time.perf_counter() with event.timestamp for better accuracy"
    This reverts commit d8d637a05a73f896a532c8c384a1dfa0e5c5f58f.
    [AdditionalEquipment.py, test_HC-SR04.py]
2026-01-11 Revert "-Distance Sensor: Replaced time.perf_counter() with event.timestamp for better accuracy"
    This reverts commit a5cd070c1240af0da3266175506db42a988bebef.
    [AdditionalEquipment.py, test_HC-SR04.py]
2026-01-11 Revert "-Distance Sensor: Replaced time.perf_counter() with event.timestamp for better accuracy"
    This reverts commit 12fae305cfe0f0c8a81411f21f1fa144f80621eb.
    [AdditionalEquipment.py, test_HRC.py]
2026-01-11 -Distance Sensor: Included distance filtering to remove outliers
2026-01-11 -Distance Sensor: Included distance filtering to remove outliers. Went back to event timestamps from Kernel -> The python side timing has too many issues under load!
    [AdditionalEquipment.py, test_HC-SR04.py]
2026-01-12 -Distance Sensor: Included sanity checks for edge detection -check_if_moving_target: Corrected smopthing logic.
    [AdditionalEquipment.py, DMN.py, test_HC-SR04.py]
2026-01-18 -Code for motion detection works fine. Removed old dist. sensor code.
2026-01-18 -Corrected Queue vs. SimpleQueue definition discrepancy
    [AdditionalEquipment.py]
2026-01-18 -Included watchdog on heartbeat to be sent from Raspi to ESP to detect Raspi crash, Python crash, com failure etc...
    [DMN.py, MotionControl.py, RobotController.cpp]
2026-01-19 -Included initiation command to arm the ESP (accounts for time diff between ESP and Raspi startup)
2026-01-19 -Corrected bug ESP in velocity setting
    [DMN.py, Gait.cpp, MotionControl.py]
2026-01-21 -Various bugfixes on ESP 32 serial communication
    [FunctionTests.cpp, Gait.cpp, MotionControl.py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]
2026-01-21 -Starting bugfix on Patrol logic
    [DMN.py]
2026-01-23 -Replaced SimpleQueue usage with Pipe connectors to reduce overhead and avoid queue up
    [AdditionalEquipment.py, DMN.py]
2026-01-23 - Corrected bug in turn around time calculation
    [MotionControl.py]
2026-02-11 - Reset AppServer. Added on_incoming_stream function to properly connect pads
    [AppServer.py]
2026-02-11 - Started fixing of DistSensor class for Trixi OS
    [AdditionalEquipment.py]
2026-02-11 - Removed Yolo26 models for now (did not work!)
    [AppServer.py]
2026-03-06 - Corrected resolution error
    [detection_engine.py]
2026-03-06 - Reverted to 11m model
    [AppServer.py]
2026-03-06 - Updated Raspi camera control to fix low light behaviour
    [detection_engine.py]
2026-03-07 - Corrected init PWM settings
    [RobotController.cpp]
2026-03-07 - Fixed WiFi power management off setup
    [system_setup.py]
